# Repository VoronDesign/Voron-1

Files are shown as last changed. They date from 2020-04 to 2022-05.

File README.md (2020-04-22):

# Voron 1.8

Voron 1.8

The official release of the Voron 1.8 3d printer.  You can find the BOM in the configurator located at the [Voron Design]( http://vorondesign.com/voron1.8) website.  The recommended sizes for this printer are 250x250x230mm and 300x300x230mm.

VORON Design

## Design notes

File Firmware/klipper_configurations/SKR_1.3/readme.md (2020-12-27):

# VORON V1.8 SKR 1.3 Config

This config file is for a BigTreeTech SKR 1.3 board on the Voron V1.8. For additional reference material, please reference BigTreeTech's Github page:

https://github.com/bigtreetech/BIGTREETECH-SKR-V1.3/tree/master/BTT%20SKR%20V1.3

Of course the discord server https://discord.com/invite/voron , specifically the channel #voron_v1_questions on it is a great place to ask questions, and has the most activity from people who have built one.

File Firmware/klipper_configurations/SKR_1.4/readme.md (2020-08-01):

<B>VORON V1.8 SKR 1.4 Config</B>

This config file is for a BigTreeTech SKR 1.4 board on the Voron V1.8. For additional reference material, please reference BigTreeTech's Github page:

https://github.com/bigtreetech/BIGTREETECH-SKR-V1.3/tree/master/BTT%20SKR%20V1.4

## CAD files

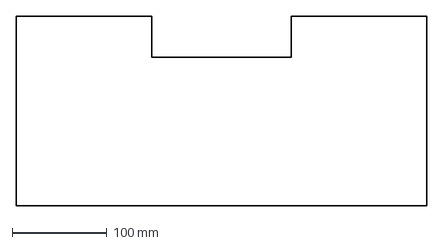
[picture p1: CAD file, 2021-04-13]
DXFs/back_panel_300mm.dxf
434.0 x 200.0 mm

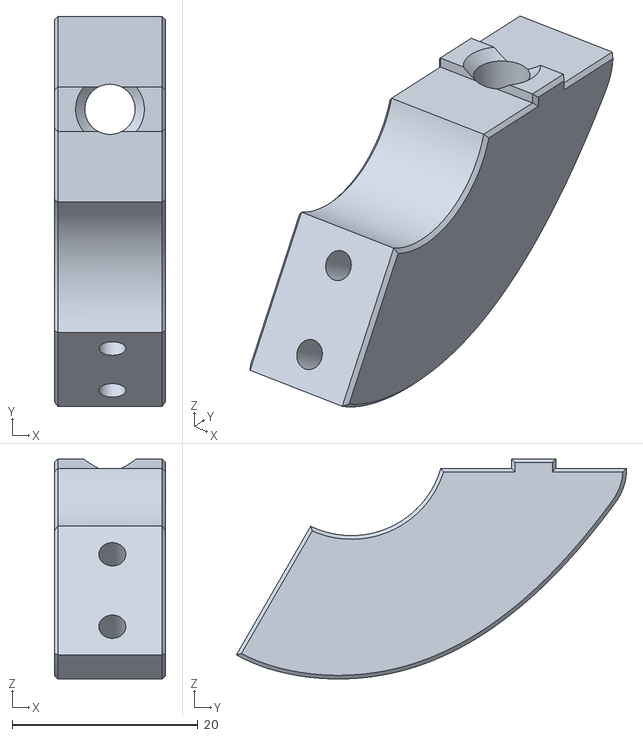
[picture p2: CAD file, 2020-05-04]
Misc/5mm STLs/display_arm_5mm_x2.stl
12.0 x 42.0 x 23.7

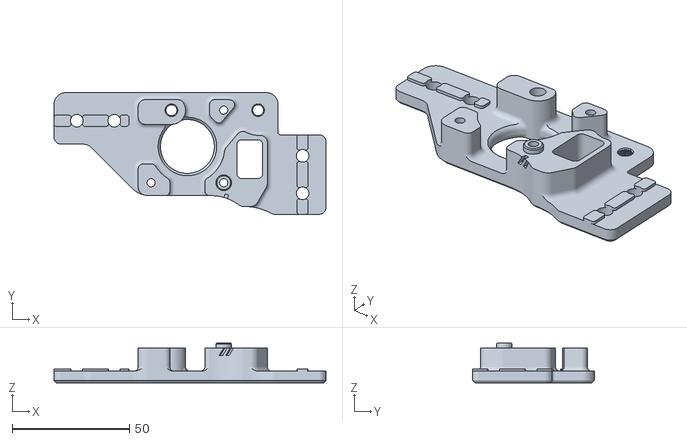
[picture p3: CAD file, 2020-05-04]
Misc/5mm STLs/Gantry/AB_Drive_Units/a_drive_frame_lower_5mm.stl
116.2 x 52.0 x 17.0

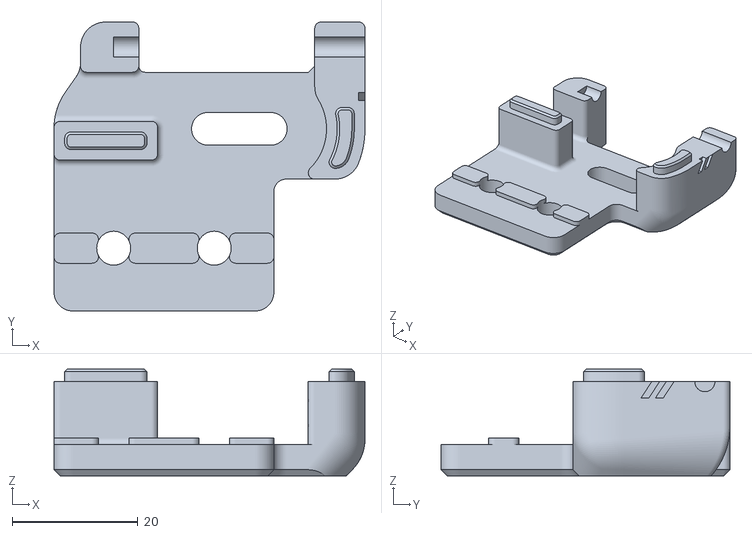
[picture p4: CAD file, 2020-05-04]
Misc/5mm STLs/Gantry/Front_Idler/front_idler_a_x2_5mm.stl
49.5 x 46.0 x 17.0

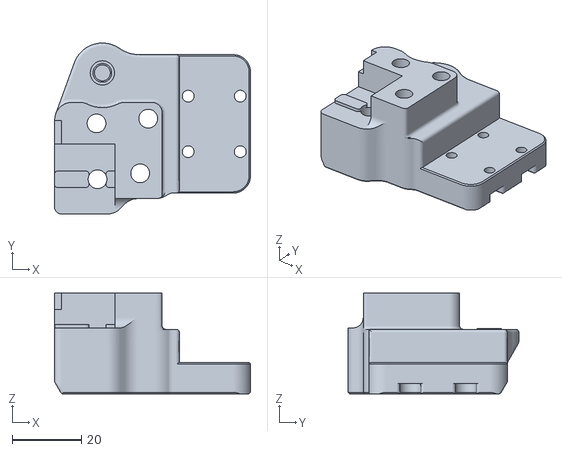
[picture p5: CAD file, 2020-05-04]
Misc/5mm STLs/Gantry/X_Axis/XY_Joint/xy_joint_right_upper_generic_chain_5mm.stl
56.5 x 49.2 x 29.0

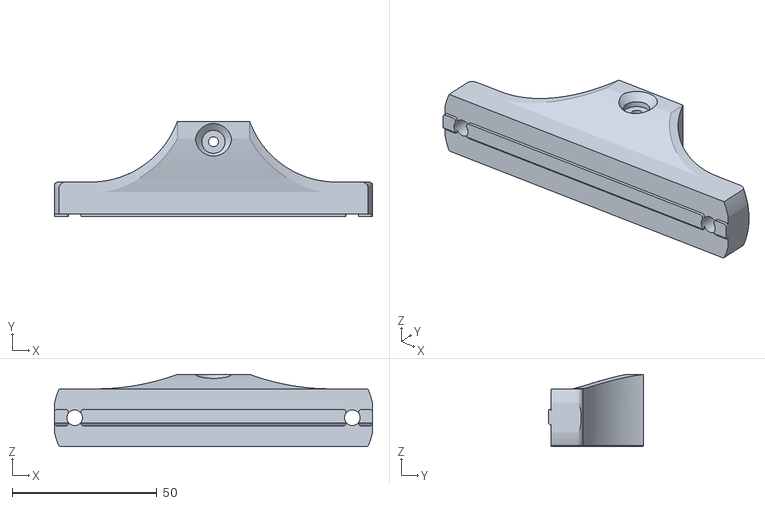
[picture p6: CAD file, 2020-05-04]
STLs/Bed/bed_mount_front.stl
109.9 x 33.0 x 25.0

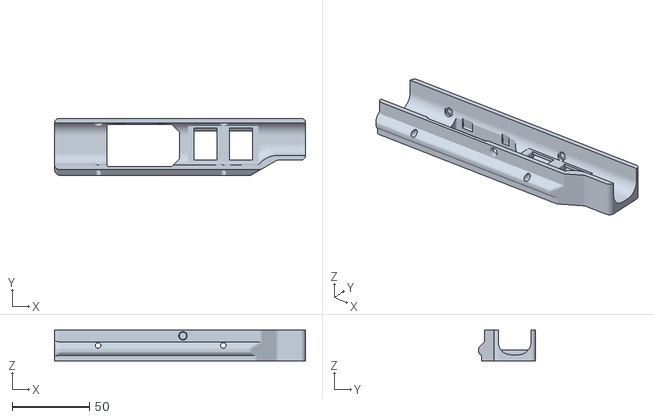
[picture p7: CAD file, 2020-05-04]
STLs/Bottom_Skirts/skirt_300_power.stl
162.6 x 37.0 x 20.0

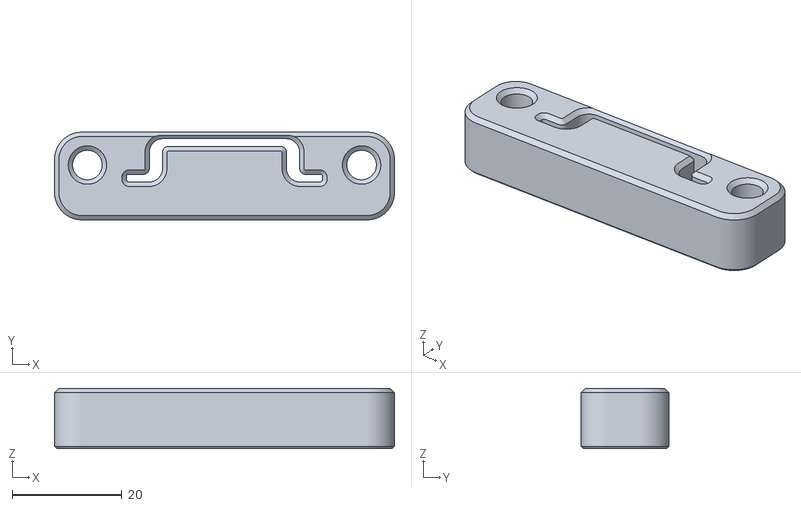
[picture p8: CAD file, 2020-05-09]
STLs/Electronics_Brackets/Bottom_Electronics_Mounting/din_inline_mount_x2.stl
62.0 x 16.0 x 11.0

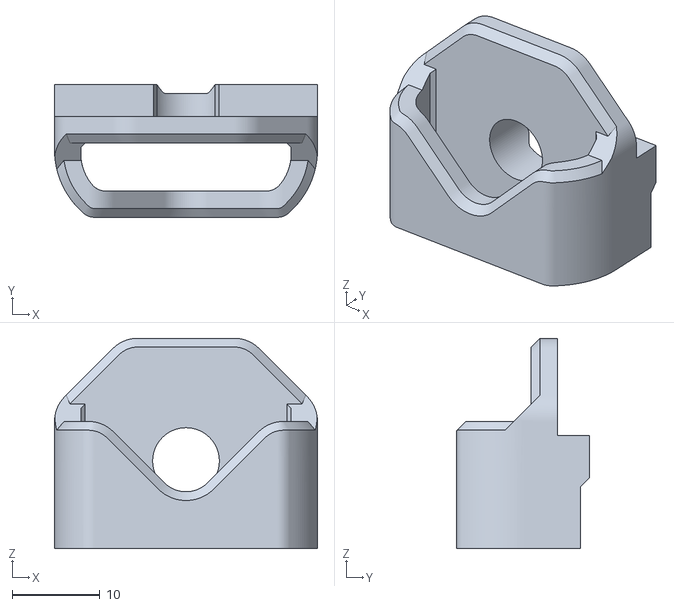
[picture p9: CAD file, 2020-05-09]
STLs/Electronics_Brackets/Rear_Electronics_Enclosure/lock_body_x2.stl
30.0 x 15.1 x 24.0

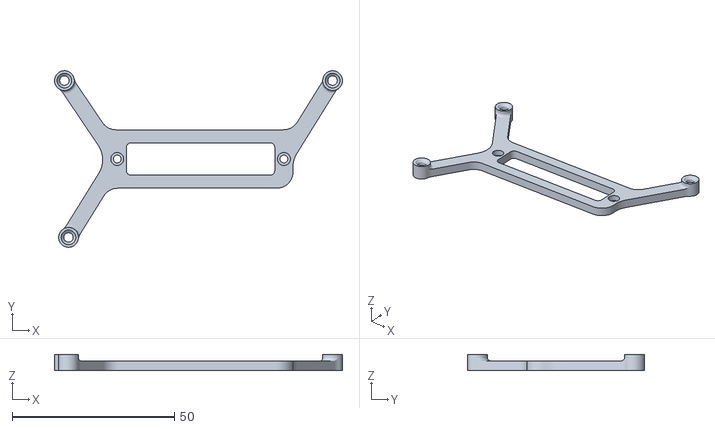
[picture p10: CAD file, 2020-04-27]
STLs/Electronics_Brackets/Rear_Electronics_Enclosure/Unsupported Controllers/ramps_bracket.stl
88.6 x 54.4 x 5.00

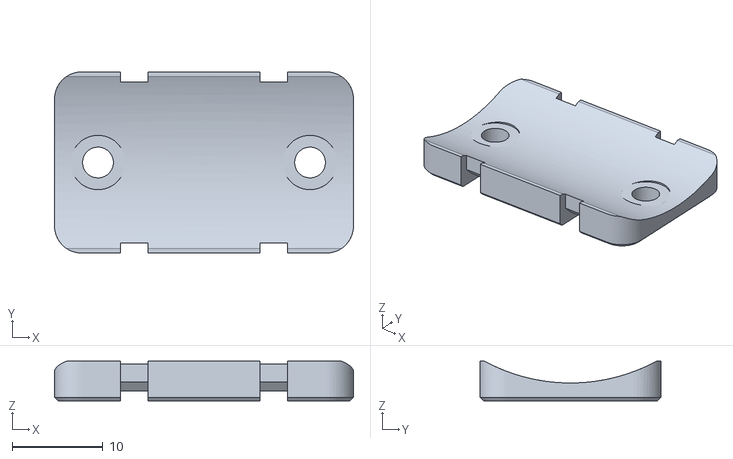
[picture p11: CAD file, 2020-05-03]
STLs/Electronics_Brackets/wire_anchor_x2.stl
33.0 x 20.0 x 4.40

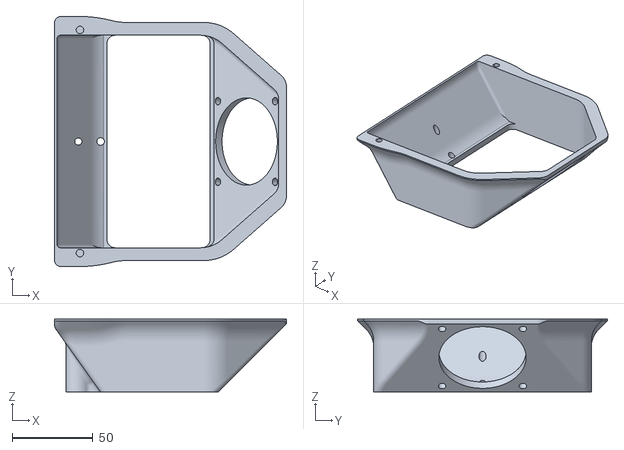
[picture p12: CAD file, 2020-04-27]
STLs/Exhaust_Filter/exhaust_filter_housing.stl
143.7 x 154.8 x 45.0

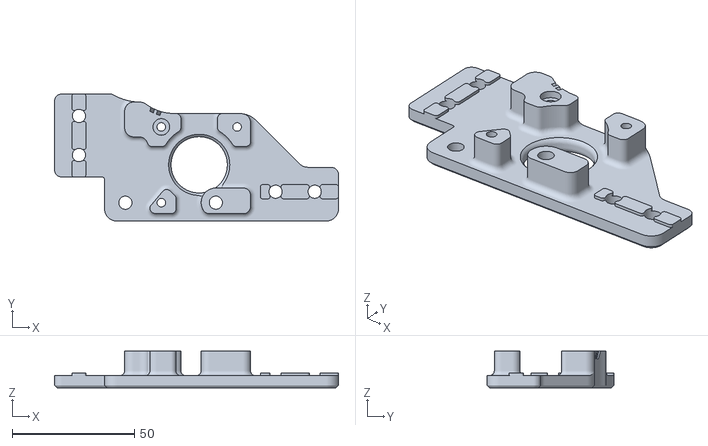
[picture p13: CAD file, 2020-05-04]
STLs/Gantry/AB_Drive_Units/b_drive_frame_upper.stl
116.2 x 52.0 x 15.0

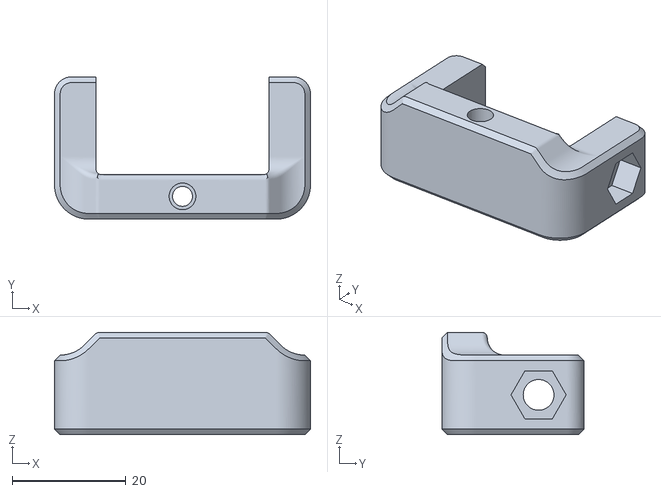
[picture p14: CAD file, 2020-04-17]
STLs/Gantry/Front_Idler/[a]_tensioner_left.stl
45.0 x 25.0 x 18.0

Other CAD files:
STLs/Electronics_Brackets/Display_Module/mini12864_arm_x2.stl
STLs/Gantry/X_Axis/X_Carriage/[a]_blower_housing_front.stl
STLs/Gantry/X_Axis/X_Carriage/Bowden/bowden_module_front.stl
STLs/Gantry/X_Axis/X_Carriage/Direct_Feed/[a]_latch.stl
DXFs/back_panel_250mm.dxf
DXFs/bottom_cover_250mm.dxf
DXFs/bottom_cover_300mm.dxf
DXFs/deck_panel_250mm.dxf
DXFs/deck_panel_300mm.dxf
DXFs/electronics_enclosure_back_250mm.dxf
DXFs/electronics_enclosure_back_300mm.dxf
DXFs/electronics_enclosure_front_250mm.dxf
DXFs/electronics_enclosure_front_300mm.dxf
DXFs/electronics_enclosure_side_250mm.dxf
DXFs/electronics_enclosure_side_300mm.dxf
DXFs/electronics_enclosure_top_250mm.dxf
DXFs/electronics_enclosure_top_300mm.dxf
Misc/5mm STLs/Bed/[a]_leadscrew_block_x2_5mm.stl
Misc/5mm STLs/Bed/bed_mount_front_5mm.stl
Misc/5mm STLs/Gantry/AB_Drive_Units/a_drive_frame_upper_5mm.stl
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

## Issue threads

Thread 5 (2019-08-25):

Not enough small bearing spacer

pasarn, 2019-08-25:
Hi Voron Team,

i have seen, i need 6 small bearing spacer. 4 for the A/B drive unit (Page 8 in the Manual) and 2 for the front idlers (Page 20 in the Manual).
From the STL filename i need 4.
`small_bearing_spacer_x4.stl`

Kriechi, 2019-08-26:
Yes - I just found the same issue. We had the same problem with the large spacers...
@volcom8190 would you mind renaming the file to `_x6.stl`?

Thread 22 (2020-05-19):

Voron 1.6 CAD

Matheusschmitz, 2020-05-19:
Where can I find the Voron 1.6 CAD files?

niolang, 2020-05-19:
They're here
https://github.com/VoronDesign/Voron-1/tree/Voron1.6

FHeilmann, 2020-08-02:
I'm going to close this issue as it seems it has been resolved. Feel free to reopen it if you're still having issues.

Closed 2020-08-02.

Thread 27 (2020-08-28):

The drill hole locations are wrong for Z axis frame with corner cubes

Nuttavoot, 2020-08-28:
I found that the top holes for Z axis frame are 20mm too low from the top when using corner cubes for Voron v1.8 and I have to drill another holes 20mm up from what define in the configurator.

jdlongenecker, 2020-09-03:
Hello @Nuttavoot, could you let me know what options you used in the configurator? I'd like to try and replicate what you did.

Nuttavoot, 2020-09-04:
> Hello @Nuttavoot, could you let me know what options you used in the configurator? I'd like to try and replicate what you did.

I use  full bom with Open build corner cubes.

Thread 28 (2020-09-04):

Missing DXFs

Annex-Engineering, 2020-09-04:
dxf files are missing for the following:

- Deck Panel (both sizes)
- Rear Panel (both sizes)
- Bottom Panel (both sizes)
- Electronics Box Panels (300 size)

natewalck, 2020-09-06:
It seems rather one-sided that Annex can use any and all Voron designs, but Annex's EULA forbids the Voron project from using anything that comes out of the Annex repo (See: https://github.com/Annex-Engineering/VORON_Mods/blob/master/LICENSE.md). It is highly unlikely this "EULA" would ever stand up in court and is clearly posturing without the basis to do so. **Feeling** like you own an idea doesn't mean you actually own it legally or have any control over said idea.

I'm not part of the Voron Design team, however I wanted to point out that this behavior violates an implicit contract within open source.. Quid pro quo is expected for opensource projects and violating this means you really have no place in a community where we share designs and ideas freely. This kind of take-without-giving-back mindset is what poisons opensource communities. I've seen it happen on many other code-based projects and I'd hate to see it happen here.

Coffee0297, 2020-09-06:
Its not for use internally in Annex so it has nothing to do with annex. The only reason the request went in is other people could use them. So not shure how it has anything to do with annex.

-Tonny

Annex-Engineering, 2020-09-06:
Your really missing the point. We were discussing on discord, and a friend of ours happened to be building a v1.8 hybrid machine and wanted some smoked acrylic panels. There are no sources for these, so someone internally offered to cut them. I'm sure there are other people with the same issue, who may or may not want to cut their own panels, and the files would help, cad or not.

natewalck, 2020-09-06:
> Its not for use internally in Annex so it has nothing to do with annex. The only reason the request went in is other people could use them. So not shure how it has anything to do with annex.
>
> -Tonny

You are right. I'm not sure why it has anything to do with Annex.

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

natewalck, 2020-09-06:
> Your really missing the point. We were discussing on discord, and a friend of ours happened to be building a v1.8 hybrid machine and wanted some smoked acrylic panels. There are no sources for these, so someone internally offered to cut them. I'm sure there are other people with the same issue, who may or may not want to cut their own panels, and the files would help, cad or not.

If someone in Voron wanted to do the same and opened a PR, would you also provide it to them? Based on the EULA, that answer would seem to be "no".

Coffee0297, 2020-09-06:
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

There is a difference between voron community and voron internals. so depends. Voron internal is a commercial entity. The community is not. So community can do what they want. voron as a commercial entity can't

-Tonny

Kirinkunhime, 2020-09-06:
What reason would there be not to provide missing files?

I've made a PCB which you can find in the Annex-repo (the Carabiner) and if the Voron-account opened an issue that some footprints for that are missing I'd gladly add them.

The EULA just states that commercial entities are not allowed to reproduce, sell and whatever, but they are free to open issues, that point out things like missing files.

To be honest, I don't understand the whole discussion here - someone pointed out that DXFs are missing. This whole discussion of the EULA of Annex, does not contribute in any way to this discussion, so I'd love if we could all cease this.
If you @natewalck are up for discussions on the matter, please drop a message on Discord & we can talk about things.

natewalck, 2020-09-06:
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

Can you link me to the Corp or LLC that Voron operates under? I am under the impression it is a group of people with a common interest, not a corporation that employs people for profit. If that impression is wrong, let me know.

ArmyAg08, 2020-09-06:
> To be honest, I don't understand the whole discussion here - someone pointed out that DXFs are missing.
> **This whole discussion of the EULA of Annex, does not contribute in any way to resolving the issue, so I'd love if we could all cease this & concentrate on the issue opened here on github.**

I don't think anyone has said they wouldn't be provided. It was possibly a simple oversight. That said, it's also probably a low priority as well. In the meantime, anyone is able to submit a PR and add them if they choose.

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

It looks like @Annex-Engineering accidentally deleted the original issue. So here it is for tracking purposes.

Closed 2020-09-06.

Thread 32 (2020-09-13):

Update SSR pins to use Neopixel connector on SKR 1.4

jdlongenecker, 2020-09-13:

jdlongenecker, 2020-09-27:
https://github.com/VoronDesign/Voron-1/pull/35

Pull request to fix this

FHeilmann, 2020-10-15:
#35 has been merged so I'll close this issue.

Closed 2020-10-15.

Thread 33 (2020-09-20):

V1.8 Manual correction on page 122

pheonix3330, 2020-09-20:
Manual says to use M3x16 screws for the panel holders but M3x8 screws are the correct size as found in the CAD model.

Closed 2020-10-25.

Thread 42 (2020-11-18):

PDF issues

sjtonic, 2020-11-18:
Some Voron v1.8 manual PDF issues:
p.32, misspelled Gantry in the title of the chapter,
p.20, screws should be M5x30 BHCS

FHeilmann, 2020-11-18:
@VoronDesign/documentation

axg20202, 2021-05-18:
The diagrams of the deck panel being mounted don't show the 20mm cutout for the bed wiring, leading some new builders to query where these are routed.

tobihille, 2021-06-26:
Not sure if this is a valid point but i'll try anyway:
I installed my dragon hotend backwards (because I was used V6 where orientation does not matter). On first heating up it melted my pl-08n probe because they both touched.
A word of caution in the docs would prevent this probably so nobody does this stupid mistake again 😅

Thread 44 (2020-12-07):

Bed size

otrava, 2020-12-07:
There is also a drawing for the bed in the document for voron 2.4. I didn't find this drawing anywhere in the documentation for Voron 1.8, so I can't continue the construction. The size as such I know is 300x300x8 mm but I am concerned with the mounting holes and their location. Would it be possible to add it to the documentation? Thank you in advance
PS I apologize for my English

J4CKT, 2020-12-17:
I just had the same problem - it's a stick in the voron_v1_questions channel.

300 Bed Drawing:
https://media.discordapp.net/attachments/551488536256184331/703610957695287316/image0.png?width=623&height=593

250 Bed Drawing:
https://cdn.discordapp.com/attachments/551488536256184331/703610958165311568/image1.png

jdlongenecker, 2021-01-16:
https://github.com/VoronDesign/Voron-1/tree/Voron1.8/Drawings

The drawings are now on Github!

Closed 2021-01-16.

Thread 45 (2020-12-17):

Fixed igus ends cause loss of X travel

J4CKT, 2020-12-17:
The fixed igus end pieces specced for the V2 cause loss of x travel in the V1.

Can the appropriate part numbers be added to the sourcing guide and the configurator for V1. Sourcing guide at least so that no one else purchases the fixed ends for a V1.

Drachenkaetzchen, 2021-05-04:
+1 on this. I'd like to see if the IGUS chains are wider to allow for other cables.

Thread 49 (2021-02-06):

Exhaust filter cutout too short

bartlammers, 2021-02-06:
In the CAD of the V1 the cutout for the exhaust filter is too short (35.6mm instead of 42mm of the V2). This carries through in the generated drawings of the top back panel. People might have gotten panels ordered or cut with a hole that's not big enough. (I have, but that doesn't matter 😄 )

bartlammers, 2021-02-06:
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
V1

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
V2

CircuitGuy, 2021-04-13:
I'm not certain, but I think @eddietheengineer has a fix for this in PR #55

bartlammers, 2021-04-13:
Yes looks like it, thanks @eddietheengineer ;)

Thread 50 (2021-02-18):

DIN Rails in configurator tied to Y instead of X extrusion length

eddietheengineer, 2021-02-18:

adelyser, 2021-02-18:
It's actually the other way around. DIN rails is tied to Y instead of X extrustion length.

eddietheengineer, 2021-02-18:
updated! :) Thanks

Closed 2022-04-27.

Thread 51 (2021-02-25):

Zip ties can interfere with homing X when Y=0

gcormier, 2021-02-25:
With the head at the front of the printer (Y=0), if the head of the zip tie is to the side, it can hit the front IDLER and prevent triggering of the X microswitch.

Routing the zip-tie in the opposite direction is rather challenging.

Closed 2023-06-22.

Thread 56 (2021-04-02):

Old release 1.8 on www.vorondesign.com

degraafm76, 2021-04-02:
When downloading STL from www.vorondesign.com the link is https://github.com/VoronDesign/Voron-1/releases/tag/V1.8 but in my opinion it should point to the latest release https://github.com/VoronDesign/Voron-1/releases/tag/V1.8r1

Sorry for posting this issue here, but i dont know how I can contact the webmaster.

Closed 2022-04-01.

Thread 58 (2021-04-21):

Some exhaust filter accented part filenames do not start with [a]_

masimplo, 2021-04-21:
Exhaust filter grill shows as red in the master cad file but is not denoted as accented in the filename.
https://github.com/VoronDesign/Voron-1/blob/Voron1.8/STLs/Exhaust_Filter/exhaust_filter_grill.stl

Same for the exhaust mount clips:
https://github.com/VoronDesign/Voron-1/blob/Voron1.8/STLs/Exhaust_Filter/exhaust_filter_mount_x2.stl

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

For the mount clips I see there is the same issue in the v2 repo also:
https://github.com/VoronDesign/Voron-2/issues/224

raymondh2, 2021-04-25:
It doesn't really matter as either works well.

Closed 2021-04-25.

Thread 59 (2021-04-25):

STL latch needed 1 time instead of 2

degraafm76, 2021-04-25:
\Voron-1-1.8r1\Voron-1-1.8r1\STLs\Panel_Mounting\Front_Doors\latch_x2.stl should be printed once according to the CAD. Filename should be changed to latch.stl

raymondh2, 2021-04-25:
Two is correct. One on top and bottom.

degraafm76, 2021-04-25:
No not for the 1.8. Please look at the master CAD. Bottom is closed with handle_bottom_left and handle_bottom_right. No latch is used.

degraafm76, 2021-04-25:
> Two is correct. One on top and bottom.

No not for the 1.8. Please look at the master CAD. Bottom is closed with handle_bottom_left and handle_bottom_right. I'm 100% sure no latch is used for bottom handles

raymondh2, 2021-04-25:
No it is still correct. The bottom handles just magnets to latch to the latch part just like the top handles

degraafm76, 2021-04-25:
I'm 100% sure it isnt the case ;-) please take a look at the master CAD and my previous screenshot. The latch would interfere with the LCD display. Maybe i can show u the issue on discord?

dubjay2k, 2021-04-25:
Confirming I only used one latch for my build, and that was at the top, where it holds magnets for the top two door handles.

Closed 2021-04-25.

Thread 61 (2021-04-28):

1.8r1 release missing many STL

jltx1, 2021-04-28:
I downloaded the official release and discovered it is missing many STL parts.  For example, the front doors are missing from panel mount directory, among other missing.

dubjay2k, 2021-04-28:
The official release would be under the `Voron1.8` branch.  It sounds like you were looking at one of the tags.

jltx1, 2021-04-28:
I used this and I know others are as well:

https://github.com/VoronDesign/Voron-1/releases/tag/V1.8r1

dubjay2k, 2021-04-28:
By default - when you visit https://github.com/VoronDesign/Voron-1 - you're in the `Voron1.8` branch. Where was that URL linked from?  They should update it.

jltx1, 2021-04-28:
from that exact repository.  For all GitHub projects they list the latest official release on the front page.  You never want to grab head unless you know what you are doing.

dubjay2k, 2021-04-28:
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
I'm seeing the front doors here.  What are the other ones that were missing?

jltx1, 2021-04-28:
I know (now) that they are in the main repository.  I downloaded the official release asset package which was clearly a mistake.  I was just pointing it out so it can be fixed so others don't run into it.

dubjay2k, 2021-04-28:
My screenshot above if from the `V1.8r1` release tag, and I'm seeing the front doors there. That was one of the STL groups that you mentioned was missing.

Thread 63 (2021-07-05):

IEC Doesn't Match BOM + Workaround Adam Tech IEC-GS-1-100

CircuitGuy, 2021-07-05:
IEC power inlet no longer matches the BOM.

Additionally, I couldn't find the 300 mm power skirt in the CAD model.

There's a few shortcomings in the CAD model. Primarily, the version included seems to be a zero-clearance fit around the intended part and is not removable.

Workaround:
On Discord, I and a few other users mentioned purchasing an Adam Tech IEC-GS-1-100, currently the part for the V0.

I'm attaching the STLs and CAD model for an updated version. The 300 mm version fits the Adam Tech IEC plug with the recommended cut-out dimensions. It engages with a loose fit and provides rear access to remove the retaining clips if needed.

Known deficiencies:
The CAD models I've attached have a fairly thin feature at the top. Ideally the plug should be slid down a mm or so. That said, the thin wall printed just fine for me.

I have provided the 250 mm version but have not tested it.

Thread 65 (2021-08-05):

Manual issue, page101

vndk36, 2021-08-05:
I noticed an issue in the sentence page 101 of the manual:
"If you cable chain as a fixed and use this end on the XY joint."
For me it should be :
"If you cable chain as a fixed **_end,_** use this end on the XY joint."

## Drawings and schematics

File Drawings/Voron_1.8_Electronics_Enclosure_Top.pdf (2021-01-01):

## 1 A

2 | 3 | 4 | 5 | 6 | 7 | 8 1 | 2

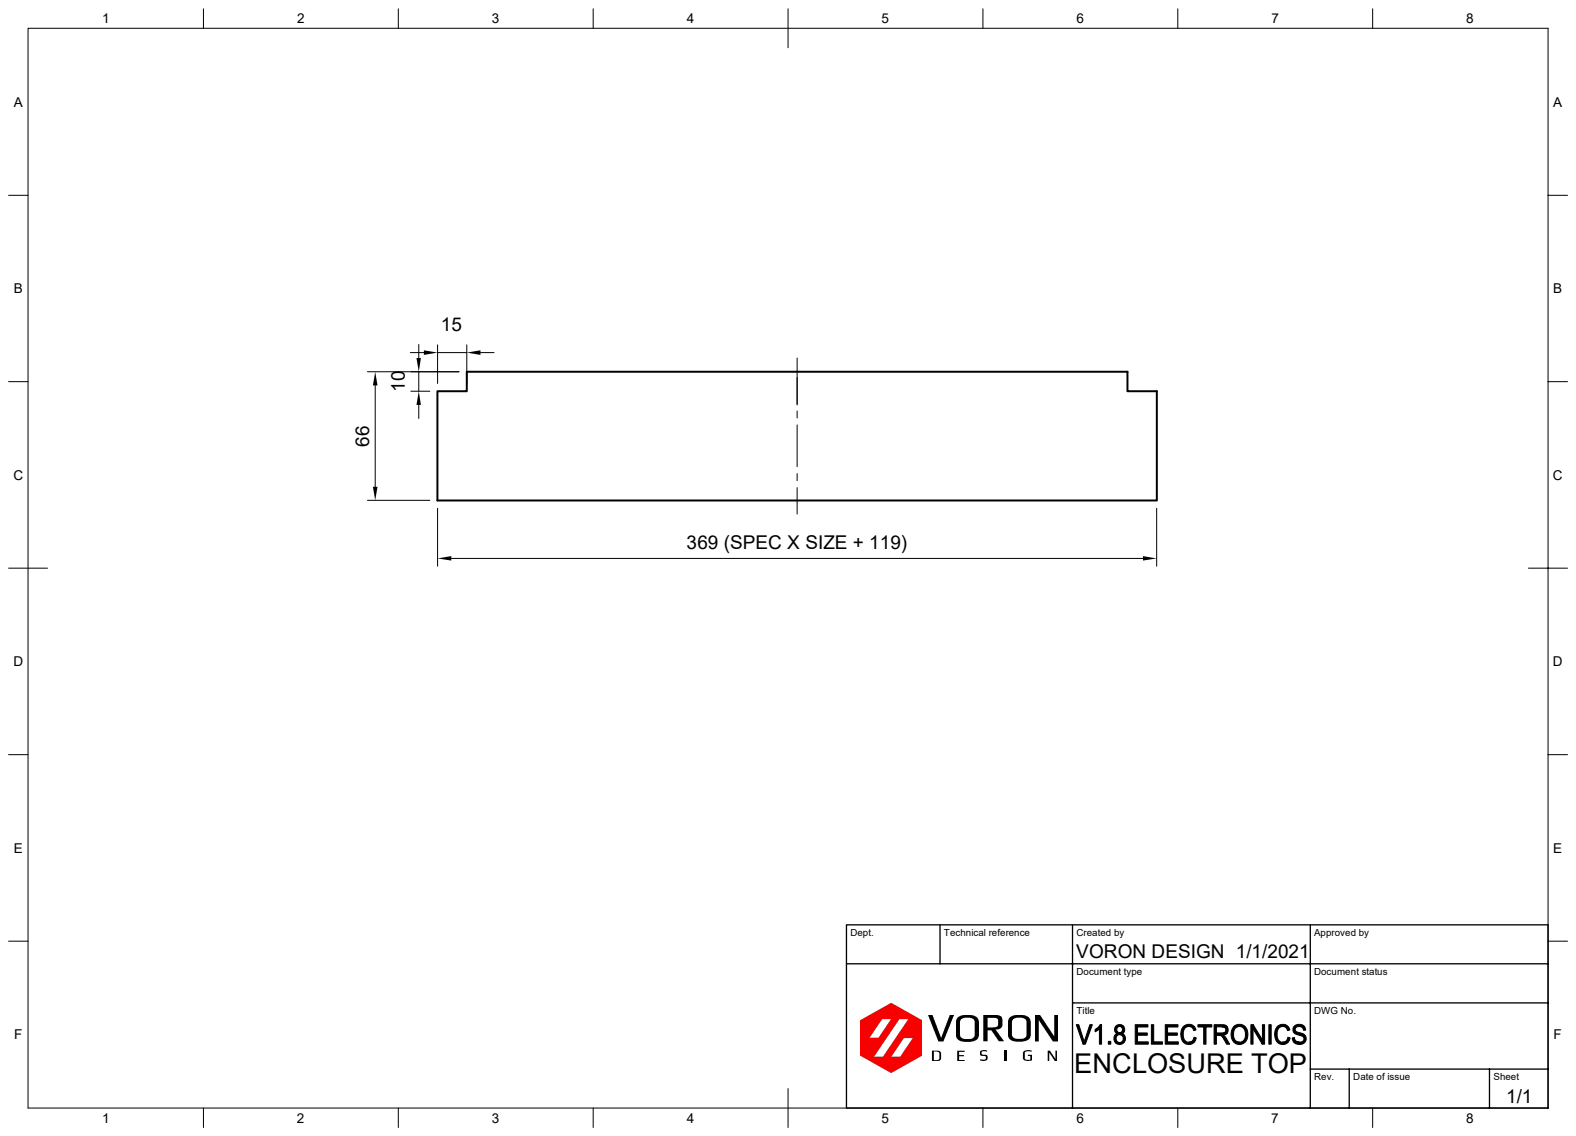
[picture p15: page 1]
F Dept.; Technical reference; Created by; Approved by Document type; Document status Title; DWG No. Rev.; Date of issue; Sheet 1/1/2021; 1/1 ENCLOSURE TOP VORON DESIGN 369 (SPEC X SIZE + 119)

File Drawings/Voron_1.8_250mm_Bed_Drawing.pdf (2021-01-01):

254

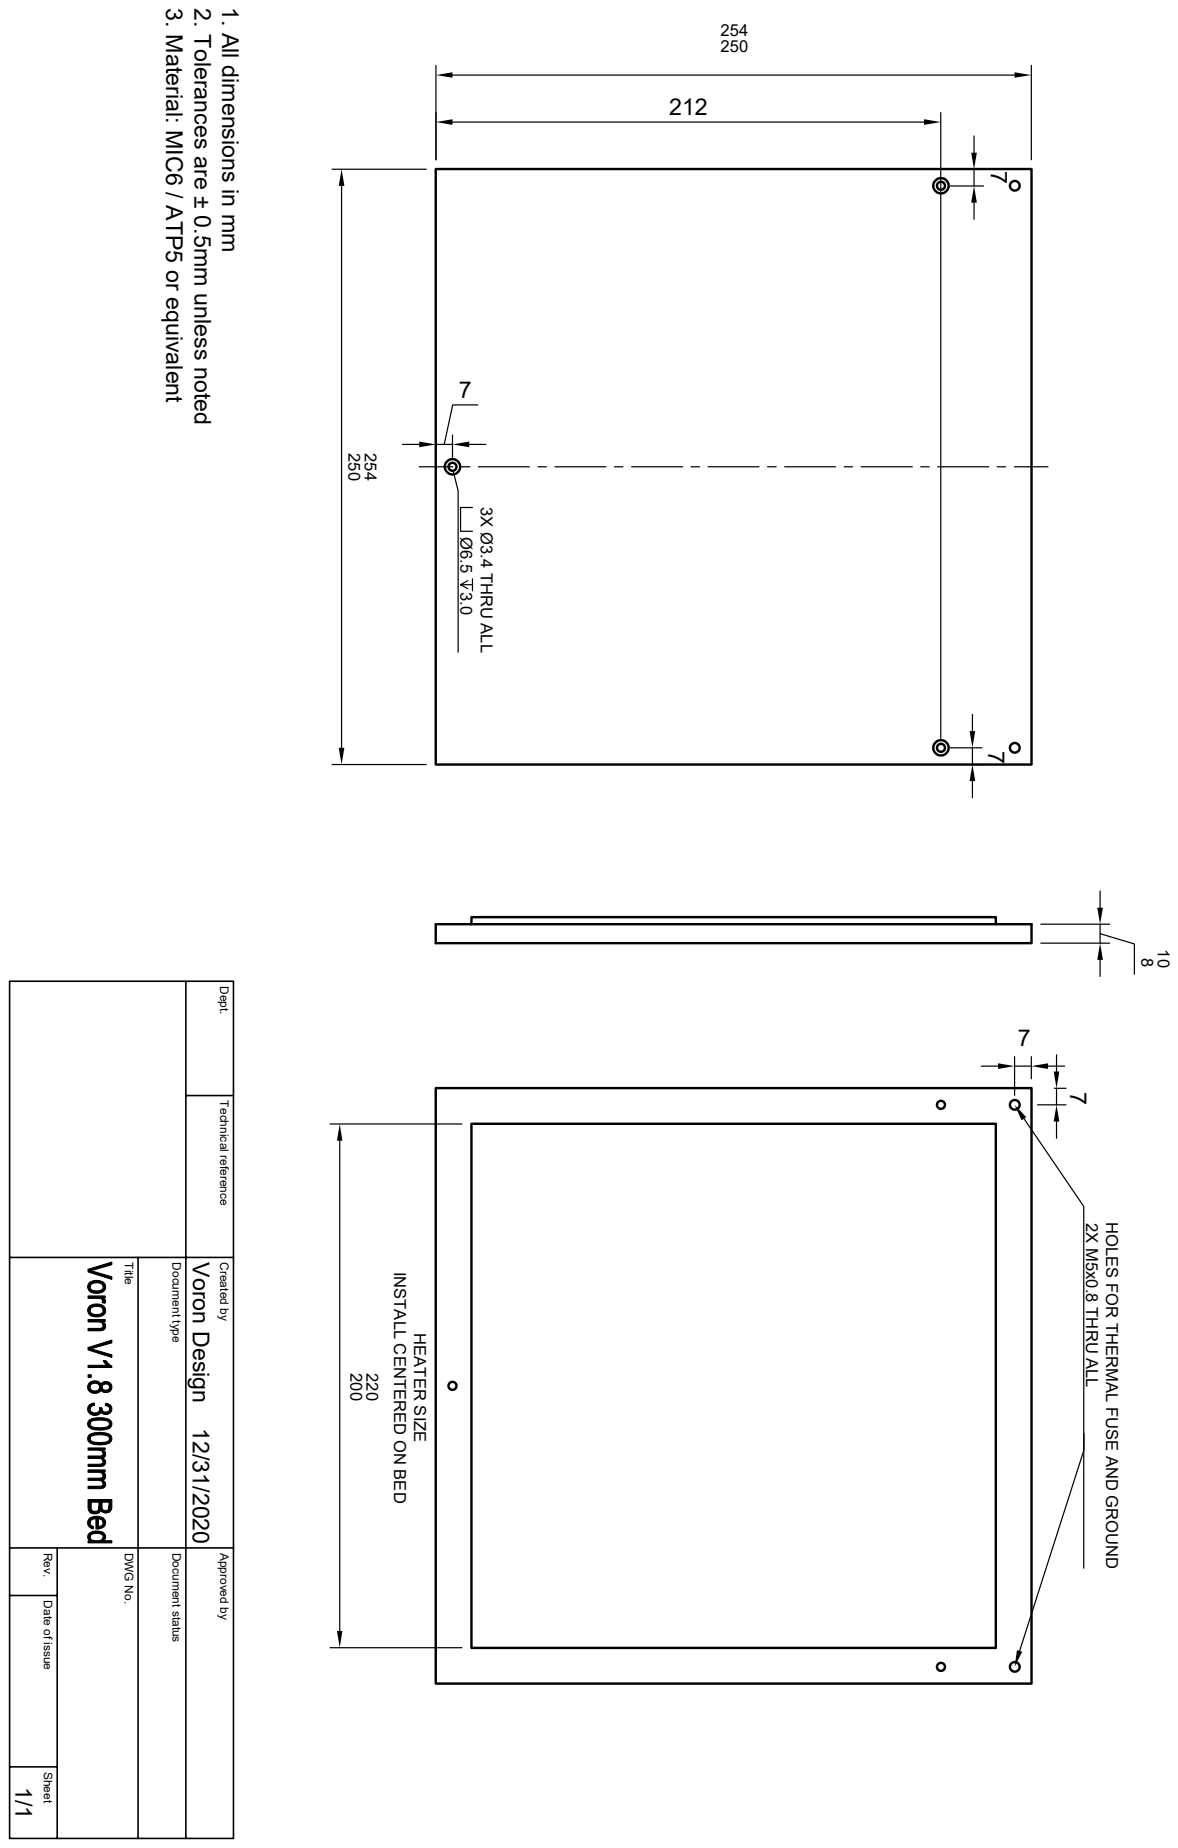
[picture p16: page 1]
7 3X Ø3.4 THRU ALL Ø6.5 3.0; 108 HEATER SIZE INSTALL CENTERED ON BED; 2X M5x0.8 THRU ALL HOLES FOR THERMAL FUSE AND GROUND ²⁰⁰ ²²⁰ 3. Material: MIC6 / ATP5 or equivalent 2. Tolerances are ± 0.5mm unless noted 1. All dimensions in mm

Dept. Technical reference Created by Approved by Title DWG No. Document type Document status Rev. Date of issue Sheet 12/31/2020 1/1 Voron Design

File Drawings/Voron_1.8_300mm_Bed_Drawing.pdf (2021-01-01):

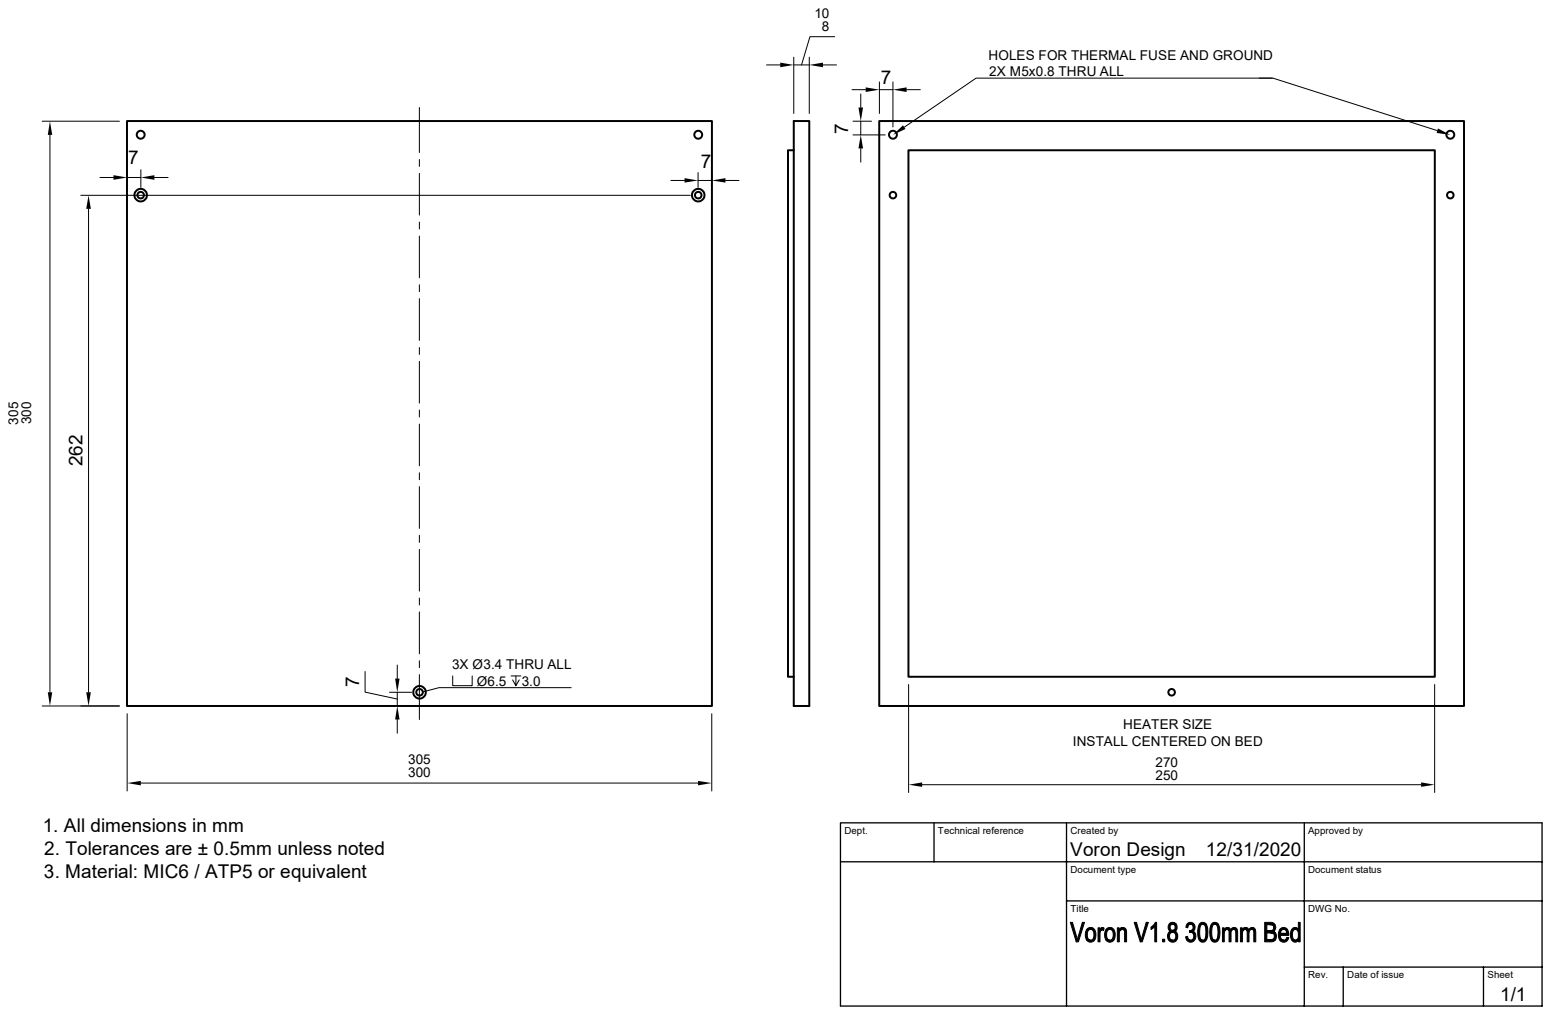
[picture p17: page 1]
Dept.; Technical reference; Created by; Approved by Document type; Document status Title; DWG No. Rev.; Date of issue; Sheet 12/31/2020; 1/1 Voron Design; 300 305 300 7 3X Ø3.4 THRU ALL Ø6.5 3.0 7 7

262 108 HEATER SIZE INSTALL CENTERED ON BED HOLES FOR THERMAL FUSE AND GROUND 2X M5x0.8 THRU ALL 270 250 1. All dimensions in mm 2. Tolerances are ± 0.5mm unless noted 3. Material: MIC6 / ATP5 or equivalent 7 7

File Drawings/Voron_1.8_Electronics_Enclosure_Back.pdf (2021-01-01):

## 1 A

2 | 3 | 4 | 5 | 6 | 7 | 8 1 | 2

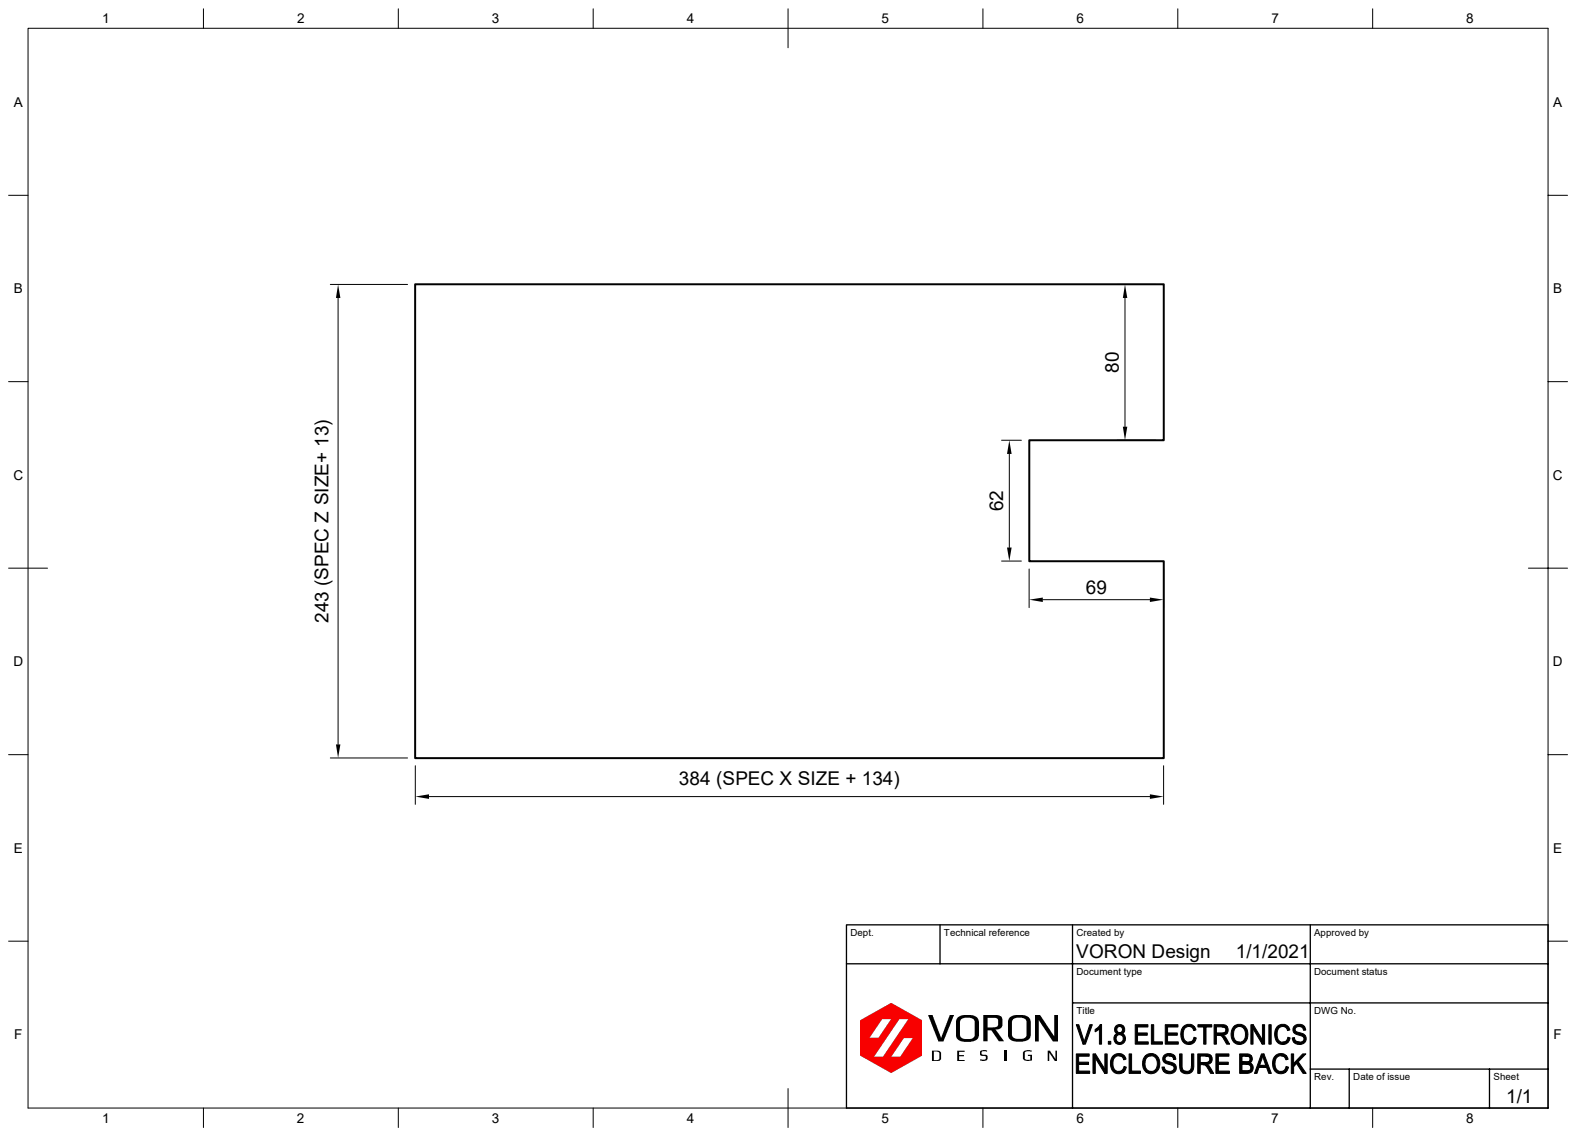
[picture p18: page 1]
F Dept.; Technical reference; Created by; Approved by Document type; Document status Title; DWG No. Rev.; Date of issue; Sheet 1/1/2021; 1/1 VORON Design

243 (SPEC Z SIZE+ 13) 384 (SPEC X SIZE + 134)

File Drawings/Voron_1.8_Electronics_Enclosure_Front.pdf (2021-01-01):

## 1 A

2 | 3 | 4 | 5 | 6 | 7 | 8 1 | 2

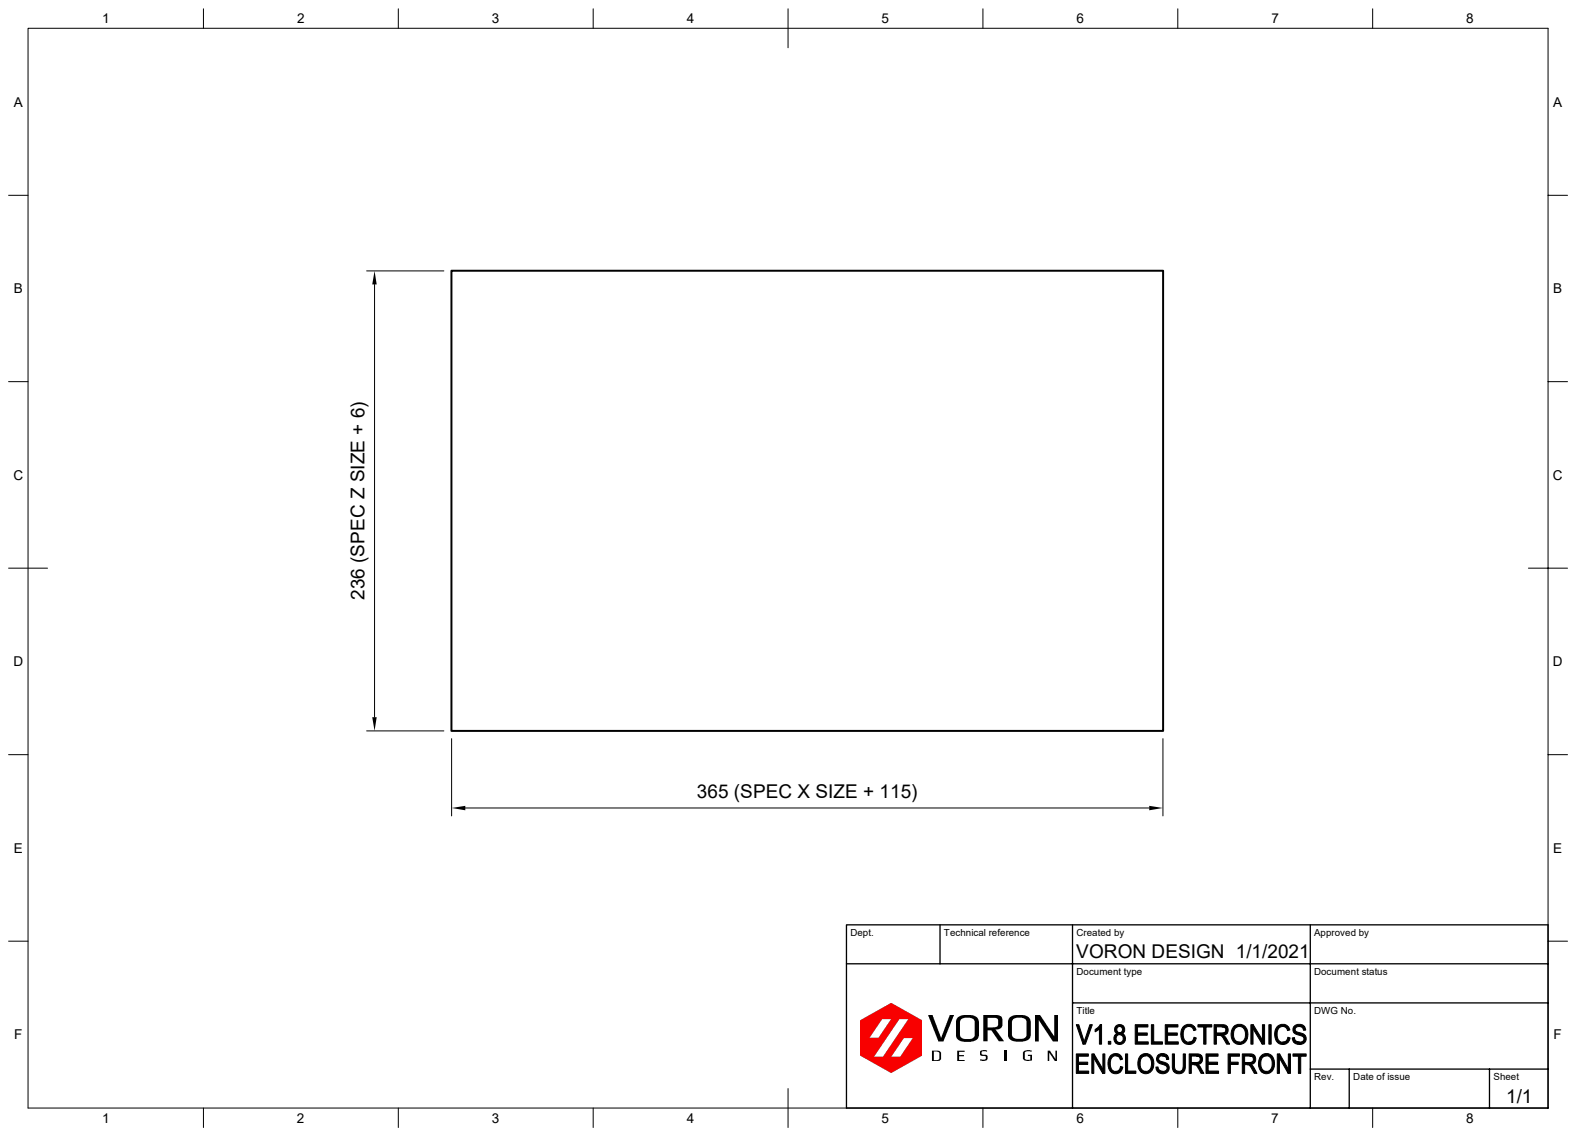
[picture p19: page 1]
F Dept.; Technical reference; Created by; Approved by Document type; Document status Title; DWG No. Rev.; Date of issue; Sheet 1/1/2021; 1/1 VORON DESIGN 365 (SPEC X SIZE + 115); 236 (SPEC Z SIZE + 6)

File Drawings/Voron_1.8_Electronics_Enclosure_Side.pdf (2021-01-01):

## 1 A

2 | 3 | 4 | 5 | 6 | 7 | 8 1 | 2

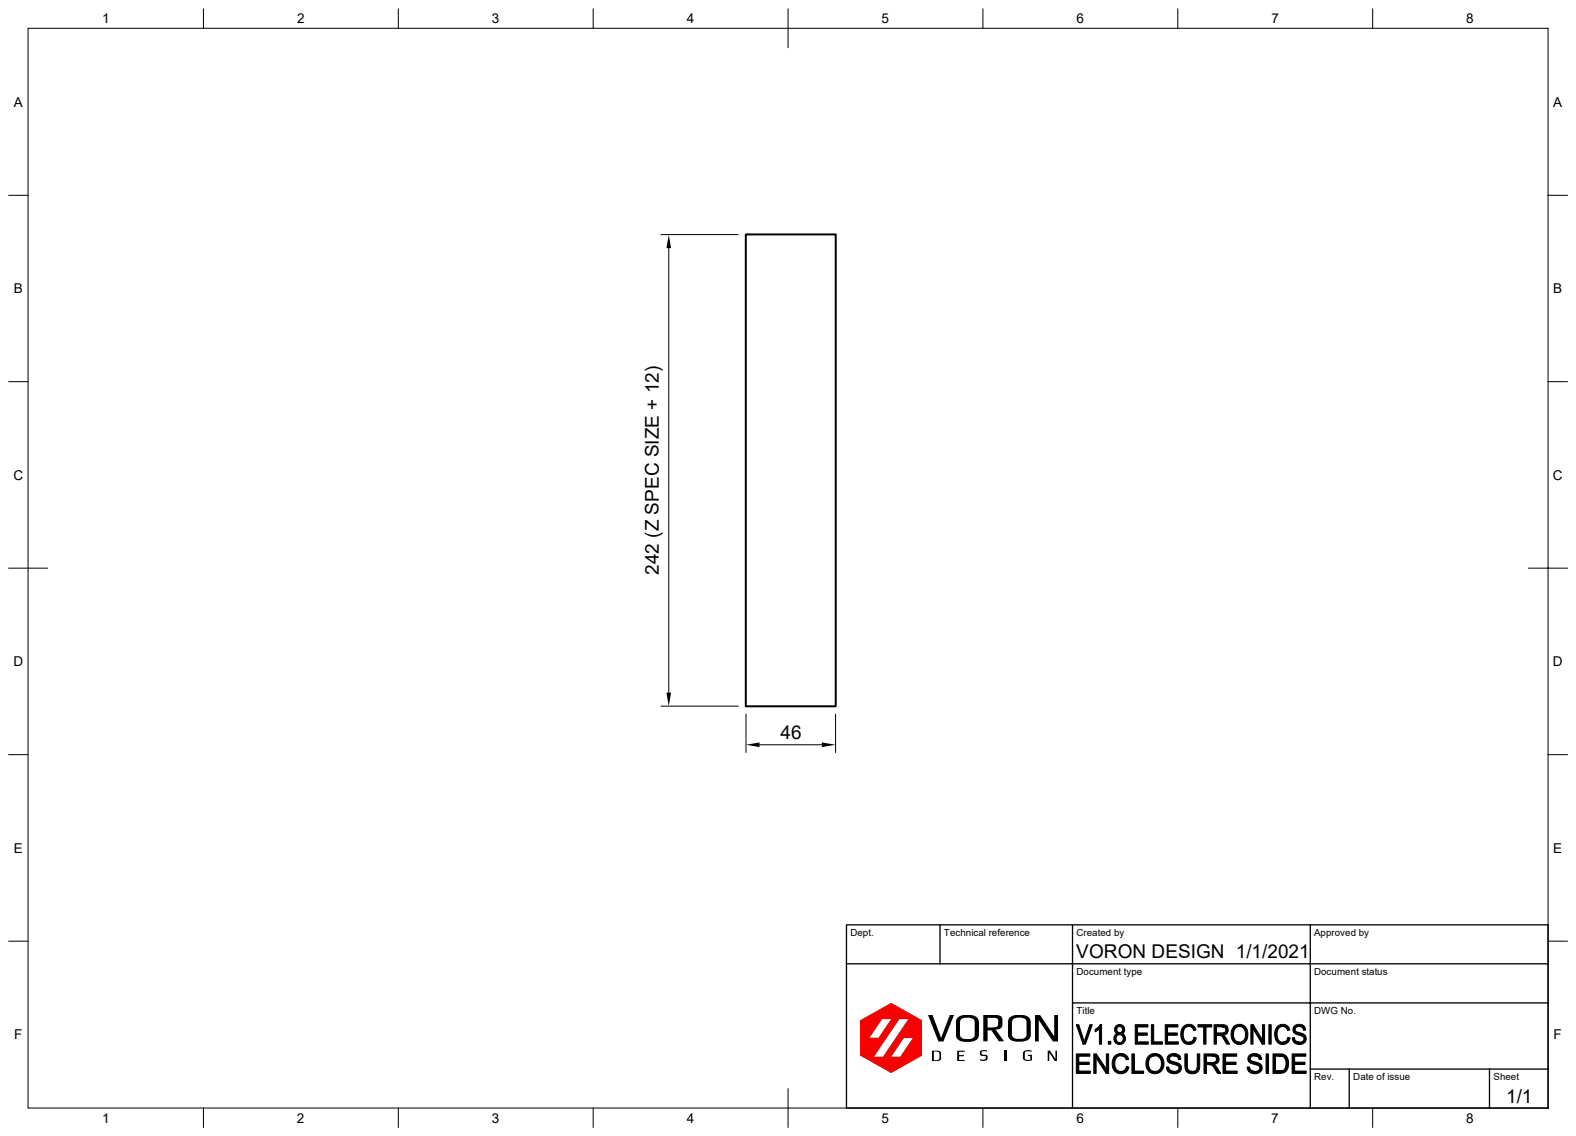
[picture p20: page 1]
F Dept.; Technical reference; Created by; Approved by Document type; Document status Title; DWG No. Rev.; Date of issue; Sheet 1/1/2021; 1/1 VORON DESIGN 46; 242 (Z SPEC SIZE + 12)

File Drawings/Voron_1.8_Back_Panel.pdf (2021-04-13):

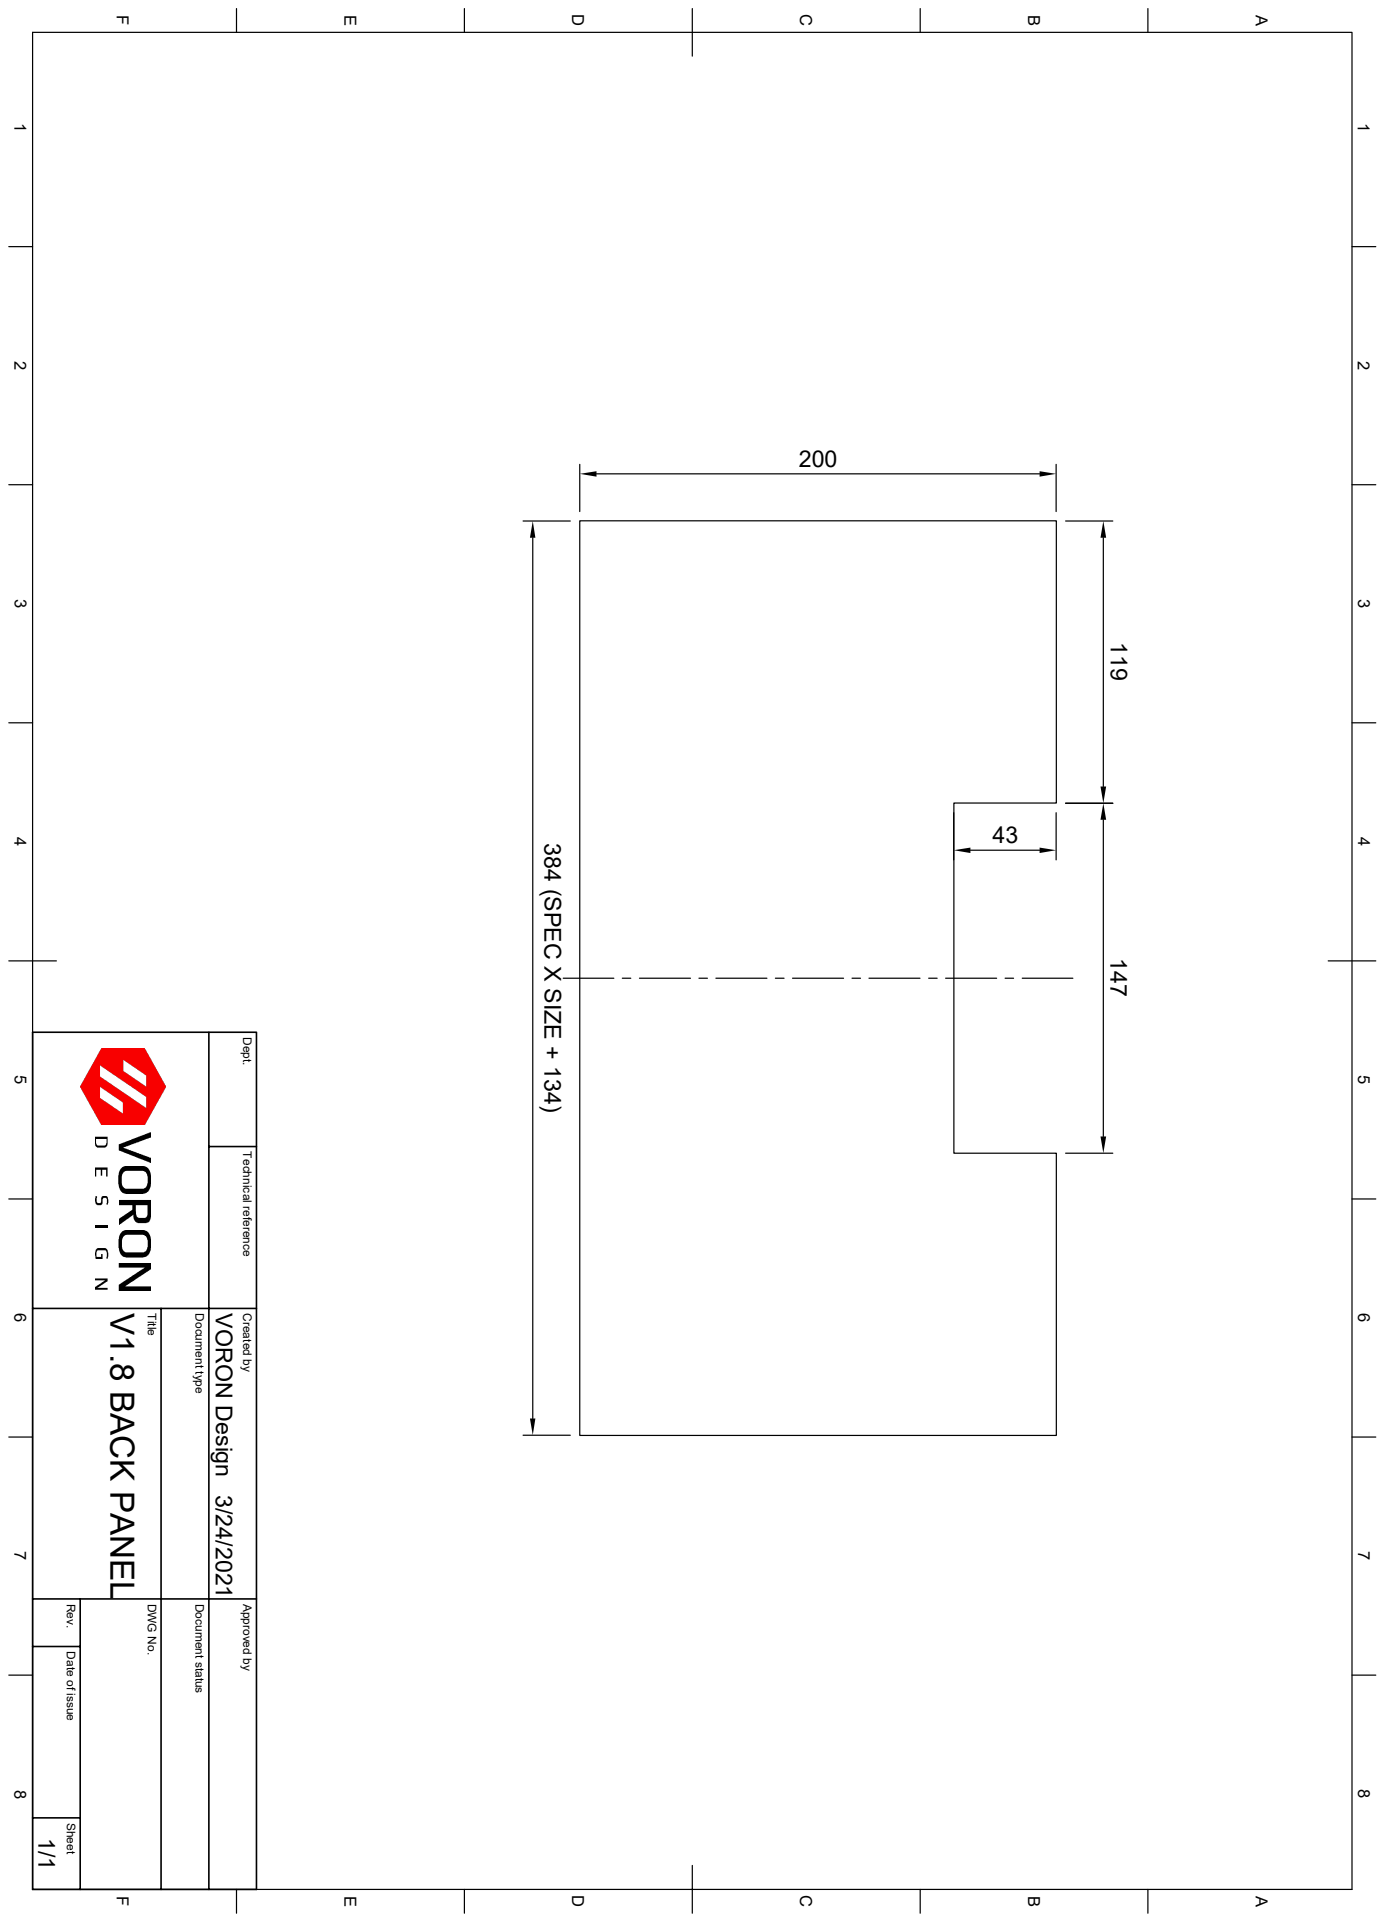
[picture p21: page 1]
200 384 (SPEC X SIZE + 134)

1 A 2 3 4 5 6 7 8 1 2 3 4 5 6 7 8 FEDCB FEDCBA Dept. Technical reference Created by Approved by Title DWG No. Document type Document status Rev. Date of issue Sheet 3/24/2021 1/1 V1.8 BACK PANEL VORON Design

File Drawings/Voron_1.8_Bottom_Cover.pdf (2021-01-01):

## 1 A

2 | 3 | 4 | 5 | 6 | 7 | 8 1 | 2

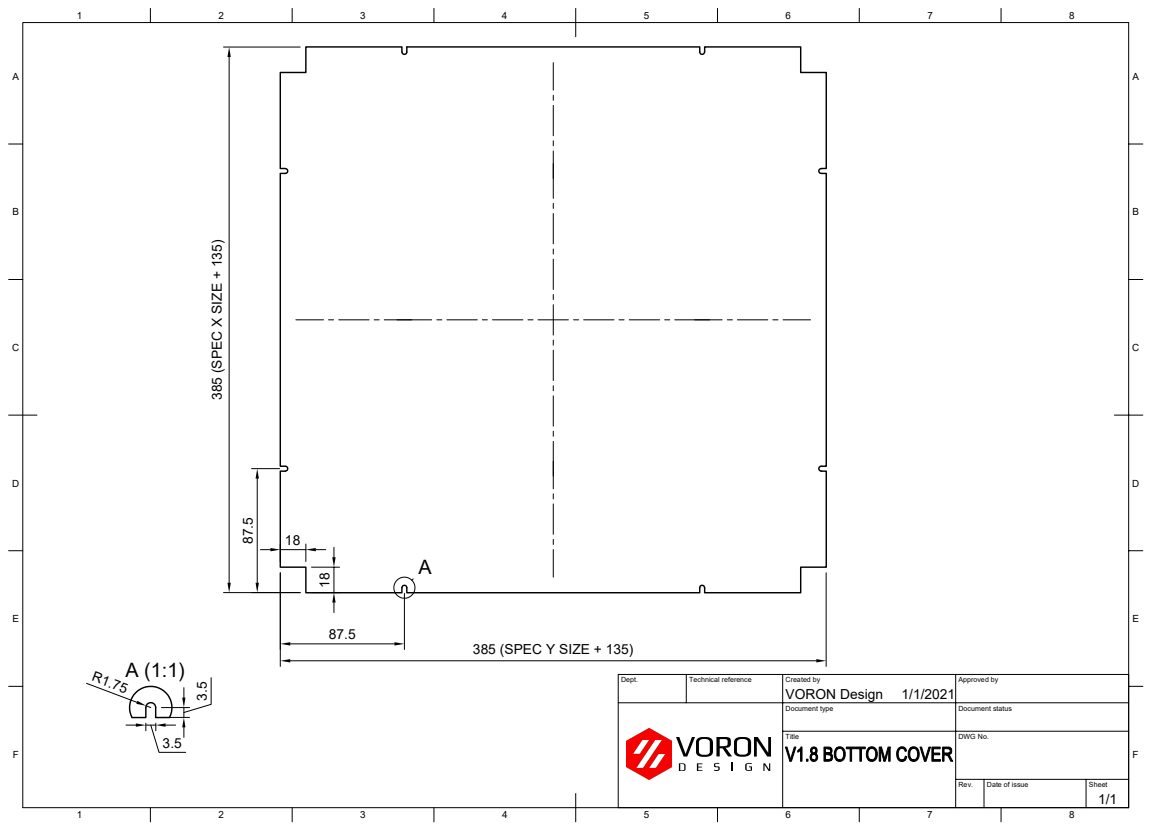
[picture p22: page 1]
F Dept.; Technical reference; Created by; Approved by Document type; Document status Title; DWG No. Rev.; Date of issue; Sheet 1/1/2021; 1/1 VORON Design; 385 (SPEC X SIZE + 135); 18 18 87.5 385 (SPEC Y SIZE + 135)

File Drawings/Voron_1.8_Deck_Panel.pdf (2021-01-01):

## 1 A

2 | 3 | 4 | 5 | 6 | 7 | 8 1 | 2

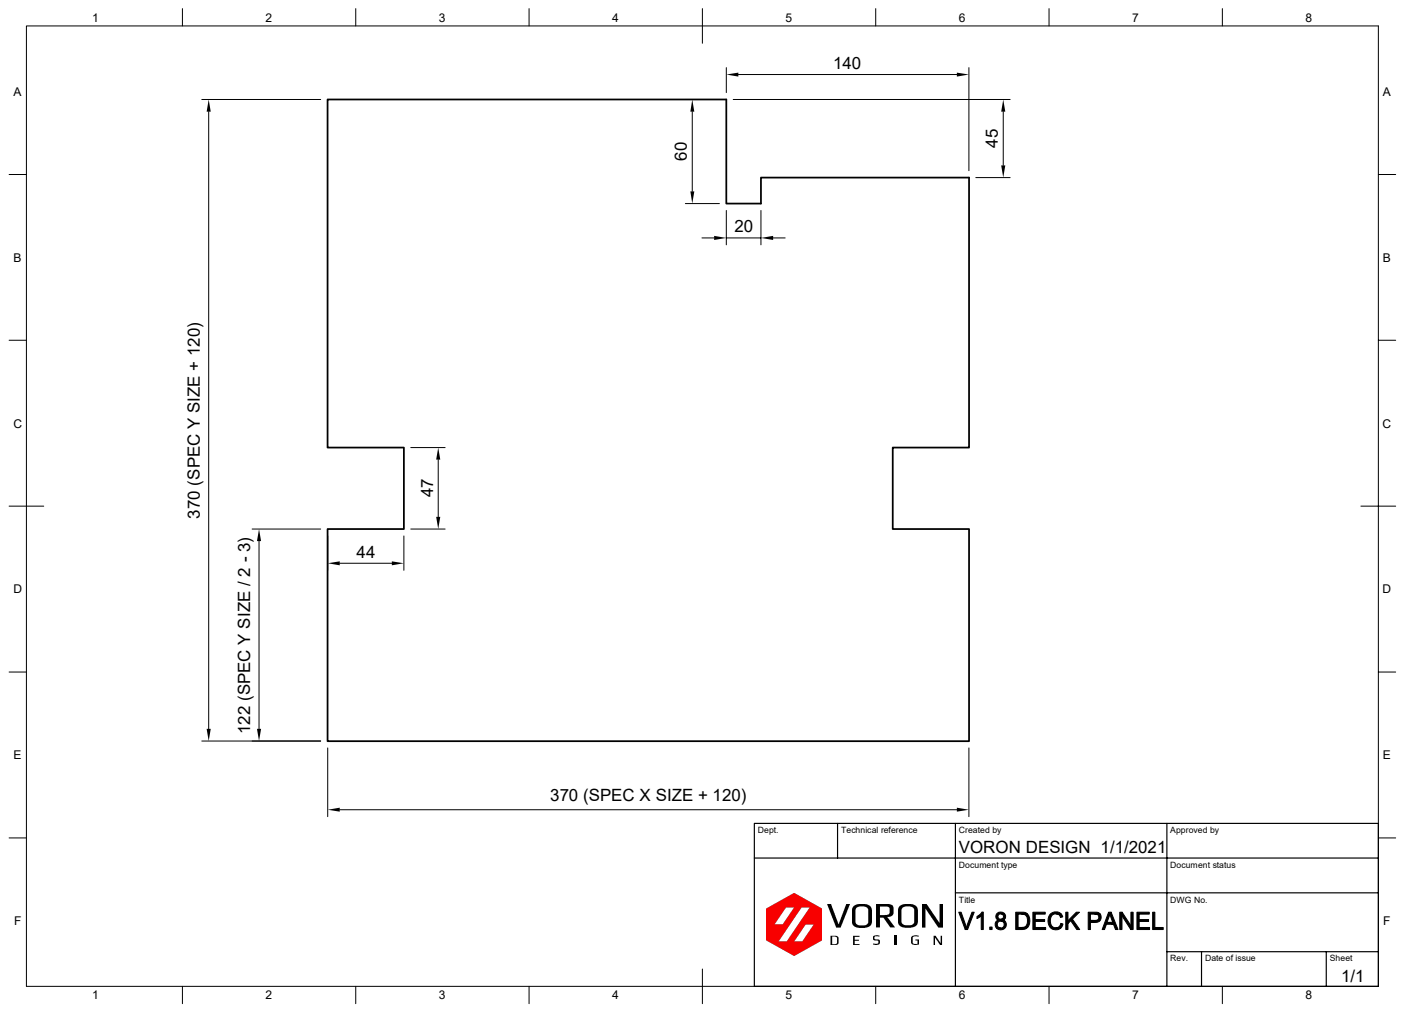
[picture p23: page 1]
F Dept.; Technical reference; Created by; Approved by Document type; Document status Title; DWG No. Rev.; Date of issue; Sheet 1/1/2021; 1/1 VORON DESIGN; 122 (SPEC Y SIZE / 2 - 3) 44

370 (SPEC Y SIZE + 120) 370 (SPEC X SIZE + 120)

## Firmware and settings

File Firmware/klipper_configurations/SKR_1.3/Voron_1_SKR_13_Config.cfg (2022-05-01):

## Voron Design VORON1.8 250/300mm SKR 1.3 TMC2209 UART config

## *** THINGS TO CHANGE/CHECK: ***
## MCU paths                            [mcu] section
## Thermistor types                     [extruder] and [heater_bed] sections - See https://www.klipper3d.org/Config_Reference.html#common-thermistors for common thermistor types
## Z Endstop Switch location            [homing_override] section
## Z Endstop Switch  offset for Z0      [stepper_z] section
## Leadscrew type settings for Z        Rotation_Distance for both steppers
## Probe points                         [z_tilt] section
## PID tune                             [extruder] and [heater_bed] sections
## Enable Heated Bed                    [Heater_bed] section
## Fine tune E steps                    [extruder] section

##========================== SKR1.3 Pin Definitions ========================
## Source: https://github.com/bigtreetech/BIGTREETECH-SKR-V1.3/blob/master/BTT%20SKR%20V1.3/hardware/SKR-V1.3-PIN.pdf
## X_STEP_PIN         2.2
## X_DIR_PIN          2.6
## X_ENABLE_PIN       2.1
## X_STOP_PIN         1.28
## E0_DET_PIN         1.29
## X_UART_PIN         1.17

## Y_STEP_PIN         0.19
## Y_DIR_PIN          0.20
## Y_ENABLE_PIN       2.8
## Y_STOP_PIN         P1.26
### E1_DET_PIN         1.29
## Y_UART_RX          1.15

## Z_STEP_PIN         0.22
## Z_DIR_PIN          2.11
## Z_ENABLE_PIN       0.21
## Z_STOP_PIN         P1.25
## PWR_DET_PIN        1.24 * This is the alternative pin used for the probe, as it provides 5v.
## Z_UART             1.8

## E0_STEP_PIN        2.13
## E0_DIR_PIN         0.11
## E0_ENABLE_PIN      2.12
## E0_UART            1.4

## E1_STEP_PIN        1.15
## E1_DIR_PIN         1.14
## E1_ENABLE_PIN      1.16
## E1_UART_RX         1.1

## HE1                2.4    
## HE0                2.7
## BED                2.5
## TH1 (H1 Temp)      0.23
## TH0 (H0 Temp)      0.24
## TB  (Bed Temp)     0.25
## FAN                2.3
## SERVO              2.0
## PROBE              0.10 * Note that the 1.3 wiring guide shifts this to a servo pin for 5V giving more compatible readouts
##===================================================================

[mcu]
##  Obtain definition by "ls -l /dev/serial/by-id/" then unplug to verify
##--------------------------------------------------------------------
serial: /dev/serial/by-id/usb-Klipper_lpc1768_0310000F43181EAEAED31252841E00F5-if00
##--------------------------------------------------------------------

[printer]
kinematics: corexy
max_velocity: 300  
max_accel: 3000
max_z_velocity: 15
max_z_accel: 50 
square_corner_velocity: 5.0  

#####################################################################
#   X/Y Stepper Settings
#####################################################################

[stepper_x]
##  Connected to X (B Motor)
step_pin: P2.2
dir_pin: !P2.6
enable_pin: !P2.1
rotation_distance: 40           #20T Pulley, 2mm Belt Pitch
microsteps: 16
full_steps_per_rotation: 200    #200 for 1.8 degree, 400 for 0.9 degree
endstop_pin: P1.28
position_min: 0
##--------------------------------------------------------------------

##  Uncomment below for 250mm build
#position_endstop: 250
#position_max: 250

##  Uncomment for 300mm build
#position_endstop: 300
#position_max: 300

##--------------------------------------------------------------------
homing_speed: 25                #Max 100
homing_retract_dist: 5
homing_positive_dir: true

[tmc2209 stepper_x]
uart_pin: P1.17
interpolate: True
run_current: 0.9
hold_current: 0.7
sense_resistor: 0.110
stealthchop_threshold: 0

[stepper_y]
##  Connected to Y (A Motor)
step_pin: P0.19
dir_pin: !P0.20
enable_pin: !P2.8
rotation_distance: 40           #20T Pulley, 2mm Belt Pitch
microsteps: 16
full_steps_per_rotation: 200    #200 for 1.8 degree, 400 for 0.9 degree
endstop_pin: P1.26
position_min: 0
##--------------------------------------------------------------------

##  Uncomment for 250mm build
#position_endstop: 250
#position_max: 250

##  Uncomment for 300mm build
#position_endstop: 300
#position_max: 300

##--------------------------------------------------------------------
homing_speed: 25                #Max 100
homing_retract_dist: 5
homing_positive_dir: true

[tmc2209 stepper_y]
uart_pin: P1.15
interpolate: True
run_current: 0.9
hold_current: 0.7
sense_resistor: 0.110
stealthchop_threshold: 0
 
#####################################################################
#   Z Stepper Settings
#####################################################################

## Z0 Stepper - Left Z Motor
## Z Stepper Socket
[stepper_z]
step_pin: P0.22
dir_pin: P2.11
enable_pin: !P0.21

# Rotation Distance for TR8x8 = 8, TR8x4 = 4, TR8x2 = 2
rotation_distance: 8            
microsteps: 16
full_steps_per_rotation: 200    #200 for 1.8 degree, 400 for 0.9 degree

endstop_pin: P1.25
##  Z-position of nozzle (in mm) to z-endstop trigger point relative to print surface (Z0)
##  (+) value = endstop above Z0, (-) value = endstop below
##  Increasing position_endstop brings nozzle closer to the bed
##  After you run Z_ENDSTOP_CALIBRATE, position_endstop will be stored at the very end of your config
position_endstop: -0.5
##--------------------------------------------------------------------

##  Uncomment below for 230mm Z
#position_max: 230

##--------------------------------------------------------------------
position_min: -5
homing_speed: 8.0 # Leadscrews are slower than 2.4, 10 is a recommended max.
second_homing_speed: 3.0
homing_retract_dist: 3.0

[tmc2209 stepper_z]
uart_pin: P1.10
interpolate: true
run_current: 0.7
hold_current: 0.5
sense_resistor: 0.110
stealthchop_threshold: 0

##  Z1 Stepper - Right Z Motor
##  E0 Stepper Socket
[stepper_z1]
step_pin: P2.13
dir_pin: P0.11
enable_pin: !P2.12
## Remember to mirror these changes in stepper_z! (there are two motors)
rotation_distance: 8            
microsteps: 16
full_steps_per_rotation: 200    #200 for 1.8 degree, 400 for 0.9 degree

[tmc2209 stepper_z1]
uart_pin: P1.8
interpolate: true
run_current: 0.7
hold_current: 0.5
sense_resistor: 0.110
stealthchop_threshold: 0

#####################################################################
#   Extruder
#####################################################################

#   Driver Socket E1
[extruder]
step_pin: P0.1
dir_pin: P0.0
enable_pin: !P0.10

rotation_distance: 22.6789511   #Bondtech 5mm Drive Gears
gear_ratio: 50:17               #BMG Gear Ratio
microsteps: 16
full_steps_per_rotation: 200    #200 for 1.8 degree, 400 for 0.9 degree

nozzle_diameter: 0.400
filament_diameter: 1.75
heater_pin: P2.7
## Check what thermistor type you have. See https://www.klipper3d.org/Config_Reference.html#common-thermistors for common thermistor types.
## Use "Generic 3950" for NTC 100k 3950 thermistors
#sensor_type:
sensor_pin: P0.24
min_temp: 10
max_temp: 270
max_power: 1.0
min_extrude_temp: 170
control = pid
pid_kp = 26.213
pid_ki = 1.304
pid_kd = 131.721
##  Try to keep pressure_advance below 1.0
pressure_advance: 0.05
##  Default is 0.040, leave stock
pressure_advance_smooth_time: 0.040

##  E1 on MCU
[tmc2209 extruder]
uart_pin: P1.1
interpolate: true
run_current: 0.5
hold_current: 0.4
sense_resistor: 0.110
stealthchop_threshold: 0

#####################################################################
#   Bed Heater
#####################################################################

[heater_bed]
##  SSR Pin - Z board, Servo Pin
heater_pin: P2.0
## Check what thermistor type you have. See https://www.klipper3d.org/Config_Reference.html#common-thermistors for common thermistor types.
## Use "Generic 3950" for Keenovo heaters
#sensor_type:
sensor_pin: P0.23
##  Adjust Max Power so your heater doesn't warp your bed
##  A good starting point is 0.4 W/cm^2
max_power: 0.6
min_temp: 0
max_temp: 120
control: pid
pid_kp: 58.437
pid_ki: 2.347
pid_kd: 363.769

#####################################################################
#   Probe
#####################################################################

[probe]
##  Inductive Probe
##  This probe is not used for Z height, only Z Tilt Adjustment
##  If your probe is NO instead of NC, add change pin to !P1.24
pin: ^P1.24
x_offset: 0
y_offset: 25.0
z_offset: 0
speed: 5.0
samples: 3
samples_result: median
sample_retract_dist: 3.0
samples_tolerance: 0.006
samples_tolerance_retries: 3

#####################################################################
#   Fan Control
#####################################################################

[heater_fan hotend_fan]
##  Hotend Fan - HE1 Connector
pin: P2.4
max_power: 1.0
kick_start_time: 0.5
heater: extruder
heater_temp: 50.0
##  If you are experiencing back flow, you can reduce fan_speed
#fan_speed: 1.0

[fan]
##  Print Cooling Fan - Fan Pin
pin: P2.3
kick_start_time: 0.5
##  Depending on your fan, you may need to increase this value
##  if your fan will not start. Can change cycle_time (increase)
##  if your fan is not able to slow down effectively
off_below: 0.10
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

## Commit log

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2018-06-05 Everything to make a Voron 1.5
    [01_home_z_mech.g, 01_physics_z_100.g, 01_physics_z_1000.g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]
2018-12-20 Cleanup for the V1.6 release
    [01_physics_z_100.g, 01_physics_z_1000.g, 02_physics_xy_1.g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]
2018-12-29 Adding missing motor covers, cleanup
    [2020 Offset Extrusion Support.STL, 80t_press_bolt_head_side.STL, 80t_press_hex_side.STL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]
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2018-12-31 Updating the name to reflect count
    [leadscrew_block_x2.stl]
2019-01-26 Updating 1.6 Klipper config to correlate to the wiring diagram
    [printer.cfg]
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2019-01-27 Updated Config to reflect Klipper changes
    [printer.cfg]
2019-04-08 Create mains_plug_panel_filter_inlet+separate_breaker_v16.STL
    add mains filtered inlet (see sourcing guide on discord for info)
    [mains_plug_panel_filter_inlet+separate_breaker_v16.STL]
2019-05-18 rev to 1.6.1
    add mosquito hotend support (see 2.1.2 release for notes)
    update filtered mains inlet to better support mounting of power supply
    add more controller mounts
    [_belt_clip_x2.stl, _coroplast_anchor_x4.stl, _jog_dial.stl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]
2019-05-23 remove nested version folder in STL directory
    [_belt_clip_x2.stl, _coroplast_anchor_x4.stl, _jog_dial.stl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]
2019-05-23 added mzbot cube and 3 test prints
    if you can print these and they thread together/look good with no issues, you can print a voron
    [MZBOT_Cube.stl, Thread Test 1.STL, Thread Test 2.STL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]
2019-05-26 add mosquito hotend sock to toolhead folder
    add mosquito hotend sock to toolhead folder
    [mosquito_sock_core_bottom.stl, mosquito_sock_core_top.stl, mosquito_sock_mold_bottom.stl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]
2019-05-26 update duet and skr mounts, add skr mini
    update duet and skr mounts, add skr mini
    [bigtree_skr_mini_single_board_mounting_frame_x2.STL, bigtree_skr_single_board_mounting_frame_x2.STL, duet_duex_single_board_mounting_frame_x2.STL]
2019-05-31 remove sn04 probe holder
    this should have not been released, testing was low
    [_z_probe_retainer_sn04_left.stl, _z_probe_retainer_sn04_right.stl]
2019-06-03 add lightbar mounts, create misc folder
    add lightbar mounts, create misc folder
    [MZBOT_Cube.stl, Thread Test 1.STL, Thread Test 2.STL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]
2019-07-16 add DXFs for bottom and deck panel for stock config for lasering
    add DXFs for bottom and deck panel for stock config for lasering
    [Bottom Panel - Stock^3.DXF, Deck Panel - Stock^3.DXF]
2019-07-17 reinforce duet and skr mounting bracket
    reinforce duet and skr mounting bracket
    [bigtree_skr_single_board_mounting_frame_x2.STL, duet_duex_single_board_mounting_frame_x2.STL]
2019-07-19 Update ramps_frame.stl
    same updates as V2 ramps frame
    [ramps_frame.stl]
2019-07-20 update v6 holder to 2.2
    forgot to do this
    [hotend_mount_front.stl, hotend_mount_rear.stl, v6_toolhead_housing_front.STL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]
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2019-08-08 update count on large bearing spacer
    update count on large bearing spacer
    [large_bearing_spacer_x6.stl]
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2019-08-21 fix removal of accent denoted parts, remove spaces in STLs
    fix removal of accent denoted parts, remove spaces in STLs
    [accent_belt_clip_x2.stl, accent_coroplast_anchor_x4.stl, accent_jog_dial.stl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]
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2019-08-21 re-add STLs
    re-add STLs
    [a_drive_lower.stl, a_drive_upper.stl, a_motor_mount.stl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]
2019-08-26 update small idler spacer quantity
    [large_bearing_spacer_x6.stl, small_idler_spacer_x6.stl]
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2019-09-19 1.6.2 - release microswitch endstop and nozzle brush holder
    this release adds the "2dot2" microswitch and an equivalent endstop holder to 1.6
    [fsr_endstop_body_a.stl, fsr_endstop_body_b.stl, fsr_strike_plate.stl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]
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2019-11-03 Adding fixed STEP using LFS
    [voron1.6_assembly.step]
2019-11-03 update bed marking template to match drawing
    update bed marking template to match drawing
    [bed_hole_marking_template_x1_Rev2.STL, bed_hole_marking_template_x1_rev1.stl]
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2019-12-22 Update printer.cfg
    Update to match SKR layout
    Remove probe as Z endstop
    [ramps.printer.cfg]
2019-12-30 Replacing the broken STEP assembly
    [voron1.6_assembly.step]
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2020-04-20 STL fixes
    [[a]_z_shaft_retainer_x8.stl]
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2020-04-26 Update 2 V2.4 files and add drilling jig
    [[a]_blower_housing_front.stl, bowen_retainer.stl, v1.8_extrusion_drilling_jig.stl]
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2020-04-27 fix bowden retainer print orientation
    [bowen_retainer.stl]
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2020-04-27 update drilling fixture to allow better alignment if printed corners are over extruded
    [v1.8_extrusion_drilling_jig.stl]
2020-04-27 add DIN mounts for common controllers, etc -- same as V2.4
    [duet_duex_bracket_x2.stl, lrs_psu_bracket_clip.stl, pcb_din_clip_x3.stl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]
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2020-05-03 add support for Gates idlers and IGUS chain
    [xy_joint_left_lower.stl, xy_joint_left_upper.stl, xy_joint_right_lower.stl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]
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2020-05-03 correct DIN bracket counts
    [duet_duex_bracket_x2.stl, lrs_psu_bracket_clip.stl, ramps_bracket_x1.stl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]
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2020-05-04 Stage2fix1 (#20)
    * fix STL orientation from earlier commit
    * Add Rear Enclosure Panel and Cooling
    * add split front door
    * reduce width of lower DIN bracket to increase clearance
    * Add initial coroplast drawings for rear electronics enclosure
    * Add 5mm Slot STLs
    * Add Fusion and STEP CAD Model
    [Electronics_Enclosure_Front_v1.DXF, Electronics_Enclosure_Sides_v1.DXF, Electronics_Enclosure_Top_v1.DXF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]
2020-05-09 update STL orientation on a few parts (#21)
    [[a]_controller_fan_guard.stl, [a]_lever_left.stl, [a]_lever_right.stl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]
2020-07-08 Fix Z Endstop (#23)
    * fix Z endstop
    * update with jst version
    [nozzle_probe.stl]
2020-08-01 SKR 1.4 configuration (#24)
    * Add initial SKR 1.4 configuration
    * add wiring diagram
    [Voron_1_SKR_14_Config.cfg]
2020-08-08 fix part orientation (#26)
    [nozzle_probe.stl]
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2020-09-09 Create Voron_1_SKR_13_Config.cfg
    Created 1.3 config based on working 1.3 config from modified 1.4 in the other folder.
    Mostly pin changes, also to homing speed.
    Heated bed is disabled by default so the user can get a working Klipper install quicker.
    [Voron_1_SKR_13_Config.cfg]
2020-09-09 cleaned conflicting references to run_current
    Hold current is just an alias for Run current, and there is confusion about the two values being set different values in the config. Cleaned up the values.
    Source for Klipper code referring to hold_current and run_current: https://github.com/KevinOConnor/klipper/issues/1850
    [Voron_1_SKR_13_Config.cfg]
2020-09-27 issue 32 and 34
    [Voron_1_SKR_14_Config.cfg]
2020-10-25 Update Assembly_Manual_1.8.pdf, fixes #33 (#38)
    #33 - Updated screw label
2020-11-16 Update SKR 1.4 config
    Lowered homing speed as the default is from 2.4 and leadscrews are slower
    Fix title and description
    Uses math to determine PRINT_END safe direction and proper parking
    Fix LCD color option
    Remove V2 references and objects from the firmware
    [Voron_1_SKR_14_Config.cfg]
2020-11-19 Merged in newer changes from the 1.4 commit mentioned by FHeilmann
    As well as:
    * Kept [probe] speed at 5.0 (stock 1.4 mentioned 10), because the stock speed is bordering on too fast for leadscrew style
    * Added labelling for what each pixel is for on the fysetc LCD Controller
    * Added labelling to indicate what each screw is for on [screws_tilt_adjust]
    * Added reference to one screw being in opposite direction for adjustment than indicated
    [Voron_1_SKR_13_Config.cfg]
2020-11-19 Added a missed gcode: to the PRINT_END macro
    [Voron_1_SKR_13_Config.cfg]
2020-11-20 Updated title to match the v1.8 board, and explanation for differing Probe pinout.
    [Voron_1_SKR_13_Config.cfg]
2020-12-31 Add DXF files for Voron 1.8 250 & 300 Deck Panels (#43)
    * Add DXF files for 250/300 Deck Panel
    * Delete Voron_1.8_Deck_Panel_300.dxf
    * Fix 300 deck panel
    [Voron_1.8_Deck_Panel_250.dxf, Voron_1.8_Deck_Panel_300.dxf]
2021-01-01 V1.8 Update - Documentation (#46)
    * sync SKR configs
    * update to step distance
    * add bed drawings
    * add panel drawings
    * add SKR 1.3 Wiring Diagram
    [Voron_1_SKR_13_Config.cfg, Voron_1_SKR_14_Config.cfg]
2021-01-21 Update SKR configs (#47)
    Removes some references to Voron 2 and updated defaults
    * Update SKR configs
    * Update SKR configs2
    * fit Z dir
    [Voron_1_SKR_13_Config.cfg, Voron_1_SKR_14_Config.cfg]
2021-01-24 Adds z_tilt config for 300mm build (#48)
    * Adds z_tilt config for 300mm build
    * Fixes 300mm z_tilt values
    * Adds z_tilt configs for 250mm & 300mm for SKR 1.3
    [Voron_1_SKR_13_Config.cfg, Voron_1_SKR_14_Config.cfg]
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2021-09-19 Homing override fixes (#67)
    * Update Voron_1_SKR_14_Config.cfg
    change homing_override default position to -10,-10 to cause error when not updated properly.
    * Update Voron_1_SKR_13_Config.cfg
    change homing_override default position to -10,-10 to cause error when not updated properly.
    * Update Voron_1_SKR_13_Config.cfg
    Comment Change
    * Update Voron_1_SKR_14_Config.cfg
    Comment Change
    [Voron_1_SKR_13_Config.cfg, Voron_1_SKR_14_Config.cfg]
2022-04-01 Renames files to correct quantity (#60)
    * Renames files to correct quantity
    * Deletes old file
    [latch.stl]
2022-05-01 Remove default sensor_types, convert tabs to spaces (#68)
    * Remove default sensor_types
    * Comment out sensor_types, convert tabs to spaces
    * Remove 3950 footnotes, ensure newlines at end of configs
    [Voron_1_SKR_13_Config.cfg, Voron_1_SKR_14_Config.cfg]
